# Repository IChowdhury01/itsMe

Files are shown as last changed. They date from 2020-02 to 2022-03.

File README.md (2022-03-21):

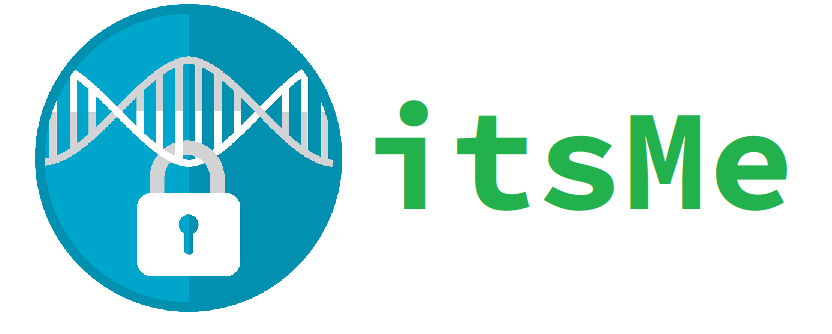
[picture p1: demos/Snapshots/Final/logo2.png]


**A new, revolutionary smart lock.**






# Project Description

itsMe is a smart lock IoT device designed for improved portability and versatility, and low cost-of-installation. itsMe locks can be 3D-printed and assembled at under $60, freely attached onto deadbolt locks with no required home renovation, and controlled remotely via Bluetooth with the itsMe Android app. itsMe's design is fully open-source, and can be modified to fit locks of any size for individual use. See our **[final presentation](https://www.youtube.com/watch?v=xuYFx85O6f8)** and **[complete documentation](/docs/full-documentation)** for further information.

# Demo
**[Operation demo](https://www.youtube.com/watch?v=Y3_GFy8Gmhg)**

**[Rotation demo](https://www.youtube.com/watch?v=DRbHsR_Iyws)**

## 3D-Printable Models

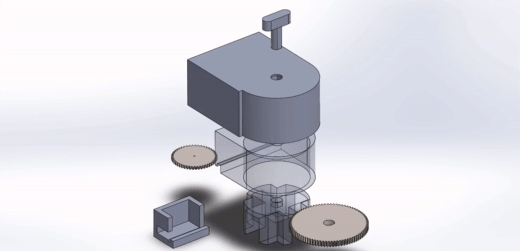
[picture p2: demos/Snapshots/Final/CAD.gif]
CAD Model


Click the animation above to find the models.

# Design

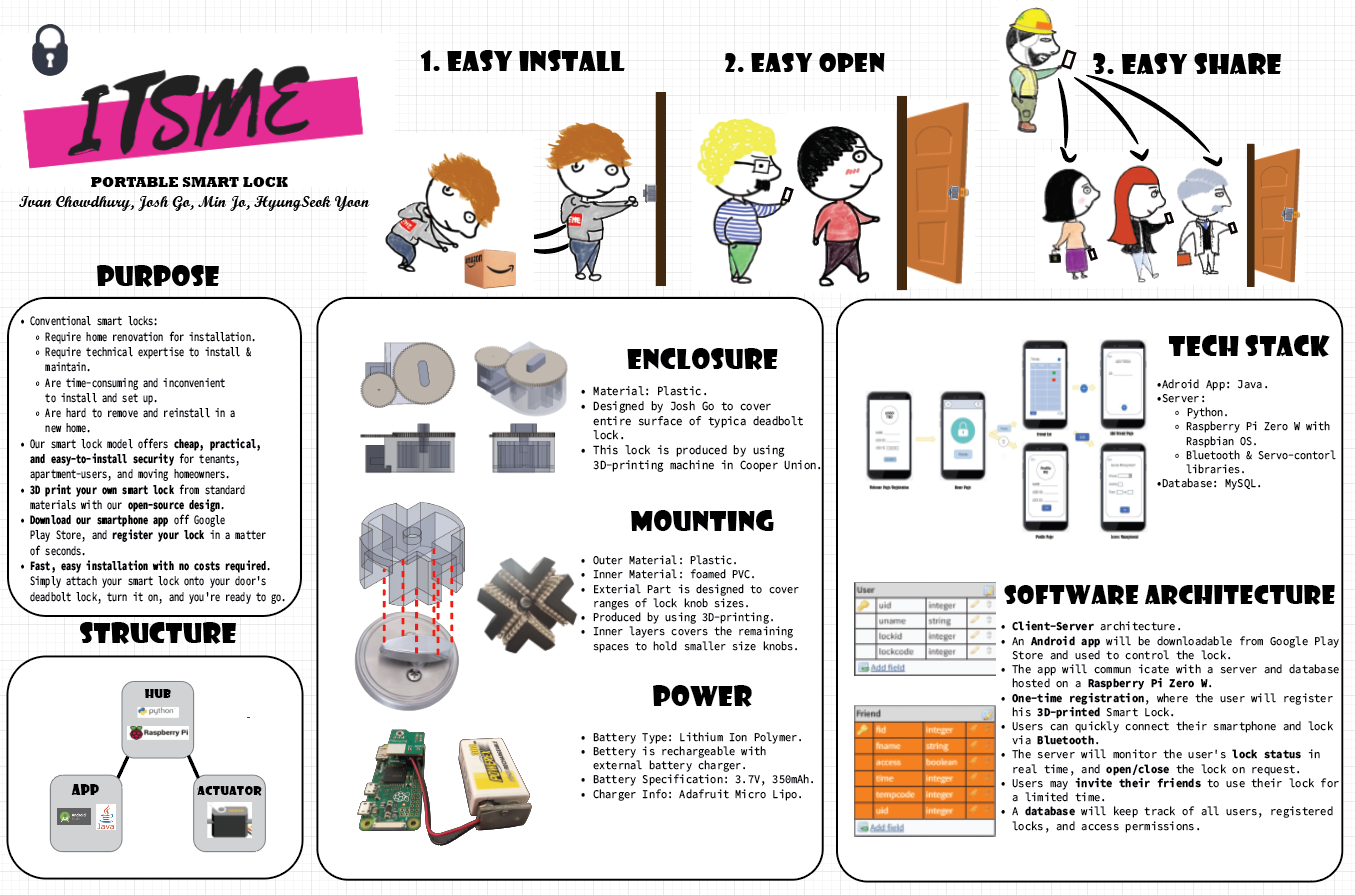
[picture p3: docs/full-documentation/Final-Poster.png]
Design Poster


## Materials


The above materials are all purchasable on Amazon. These are the recommended brands minimizing cost-of-installation; other brands may work, but device stability will not be guaranteed. 

# Getting Started

## Prerequisites
- Android phone
- [Android Studio 4.0+](https://developer.android.com/studio) installed.

## Installation
1. Purchase the materials listed above.
2. Clone this repository
3. [Optional] Modify the dimensions of the downloaded CAD models to suit your needs.
4. 3D print your materials with ABS plastic.
5. Assemble your 3D-printed parts, following the animation above. Place the Servo Motor in the groove and wire it to your Raspberry Pi. Place the self-adhesive tape strips around the edge of your device (where it'll make contact with the door).
6. Open this project in Android studio. Then connect your Android device to your computer with a USB cable, and run the app. Your phone will now have the itsMe app installed.

## Usage
1. Install your smart lock onto your door by simply placing the grip over a pre-existing deadbolt lock. Make sure itthe device is firmly attached to the door with the adhesive strips.
2. Open the itsMe Android app.
3. Turn on Bluetooth on your phone and connect it to your smart lock.
4. Your lock's state is now being monitored through the app. Press the "Lock" or "Unlock" app buttons to control the lock's state. Enjoy!

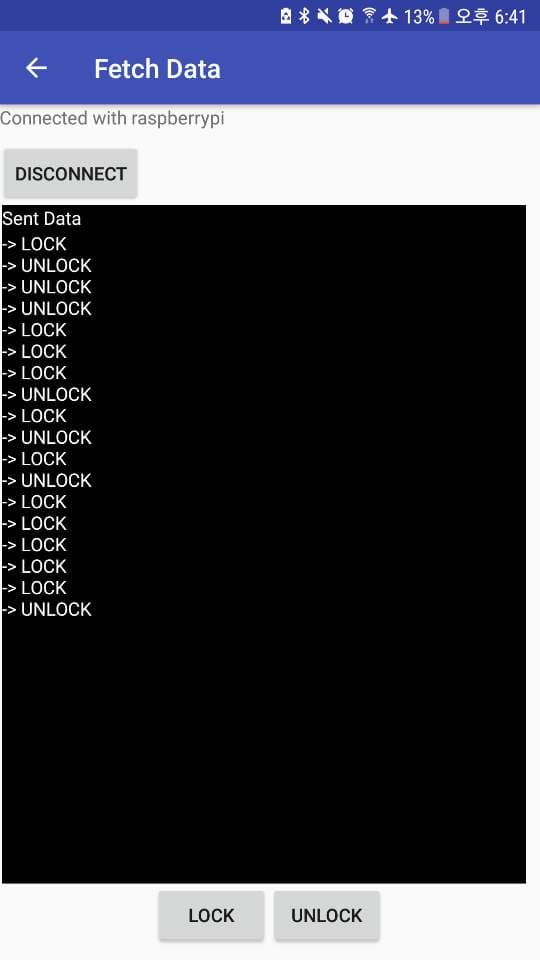
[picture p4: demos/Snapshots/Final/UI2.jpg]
UI


# License

This project is licensed under the MIT License - see the [LICENSE](LICENSE) file for details

# Acknowledgements

- **Development team**: Min JO, Hyungseok Yoon, Josh Go, Ivan Chowdhury
- **Advisors:** Sam Keene, Carl Sable, Shivam Mevawala

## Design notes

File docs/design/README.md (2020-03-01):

# Design Summary

## Purpose

- Conventional smart locks:
  - Require home renovation for installation.
  - Require technical expertise to install & maintain.
  - Are time-consuming and inconvenient to install and set up.
  - Are hard to remove and reinstall in a new home.
  - Have high server-maintenance fees.
- Our smart lock model offers **cheap, practical, and easy-to-install security** for tenants, apartment-users, and moving homeowners.
- **3D print your own smart lock** from standard materials with our **open-source design**.
- **Download our smartphone app** off Google Play Store, and **register your lock** in a matter of seconds.
- **Fast, easy installation with no costs required.** Simply attach your smart lock onto your door's deadbolt lock, turn it on, and you're ready to go.

## Software Architecture

- **Client-Server** architecture.
- An **Android app** will be downloadable from Google Play Store and used to control the lock.
- The app will communicate with a **server** and **database** hosted on a **Raspberry Pi Zero W**.
- **One-time registration,** where the user will register his **3D-printed** Smart Lock.
- Users can quickly connect their smartphone and lock via **Bluetooth**.
- The server will monitor the user's **lock status** in real time, and **open/close** the lock on request.
- Users may **invite their friends** to use their lock for a limited time.
- A **database** will keep track of all users, registered locks, and access permissions.

## Tech Stack

- Android App: 
  - Java
- Server: 
  - Python
  - Raspberry Pi Zero W with Raspbian OS.
  - Bluetooth & Servo-controller libraries
- Database: 
  - MySQL

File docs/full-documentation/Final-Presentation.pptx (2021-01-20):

## ItsMe: Portable Smart Lock

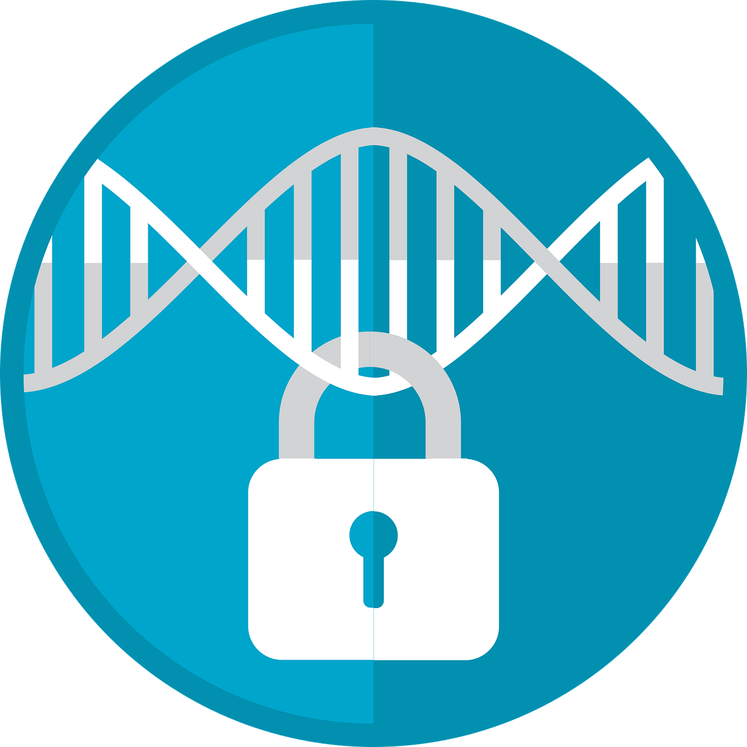
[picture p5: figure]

Hyungseok Yoon, Min JO,
Ivan Chowdhury, Josh Go

## Purpose

- Project: A portable, attachable smart lock for doors with deadbolt locks.
- Catered towards tenants, apartment-users, and frequently moving homeowners.
- Main features
  - Fast, attachment-based installation requires no home renovation.
  - Open-source, modular design
  - 3D-printable
- Other Features
  - Adjustable to most lock sizes.
  - Low manufacturing cost
  - Supports manual and remote unlocking.
  - Android application: used to monitor and lock/unlock door.

## Project Design

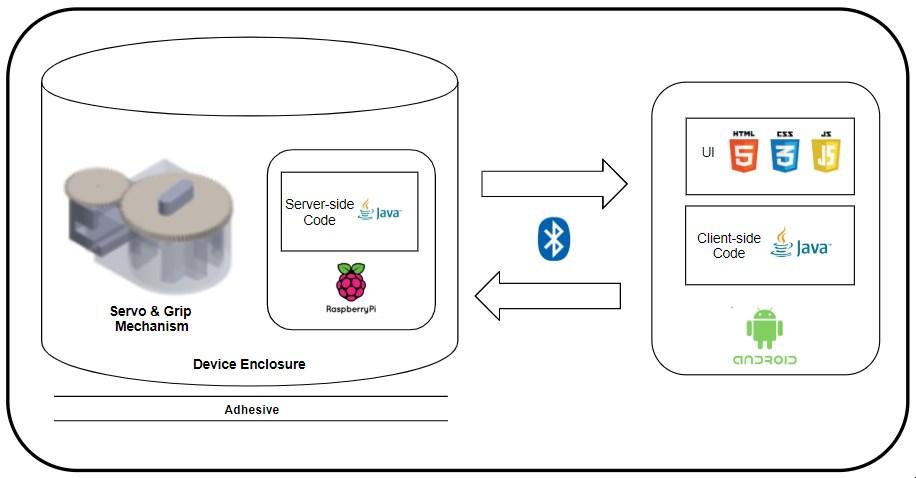
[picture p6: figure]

- App and device communicate via Bluetooth Low Energy
- Raspberry Pi and Servo connected directly.
- 3D-printed gripping mechanism and enclosure.
- Double-sided adhesive tape used to attach onto door.

## Prototype: Specs

- Lightweight:
  - Gripping mechanism: ~150g
  - Overall device: ~250g
- Manufacturing cost: ~$60.00
- Contains slot for Servo motor.
- Smooth-fit groove allows for easy fit with multiple deadbolt lock sizes.
- Manual lock control supported by rotating knob.


## Prototype: Cost of Materials

Material/Process | Cost Estimate
Raspberry Pi Zero W | $10.00
Adafruit Feedback 360° Servo | $27.99
3D-printing (ABS plastic) | $5-10
Strenco 2” Self Adhesive Tape Strips | $13.50

Manufacturing cost: ~$60.00

## Status Update

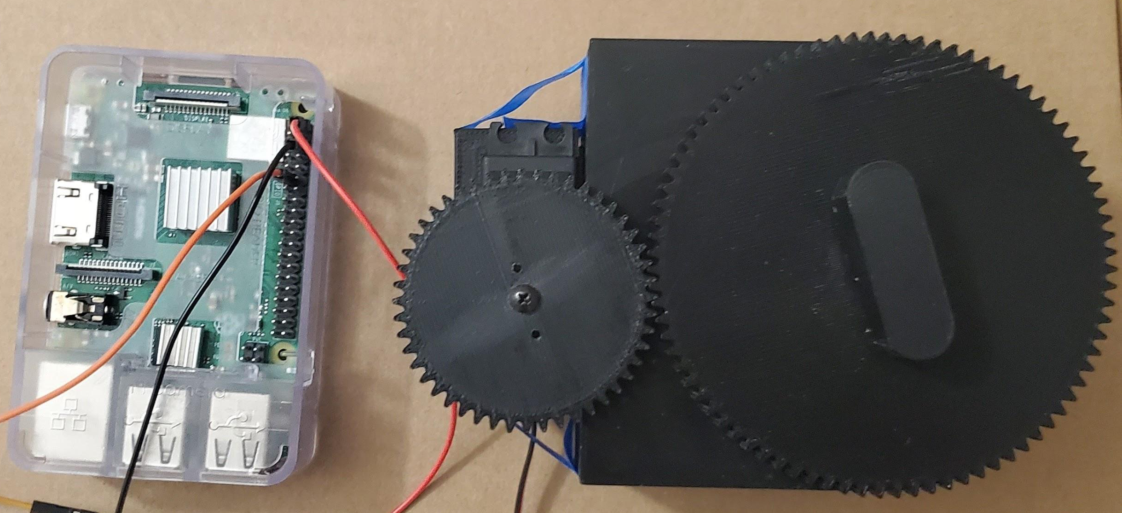
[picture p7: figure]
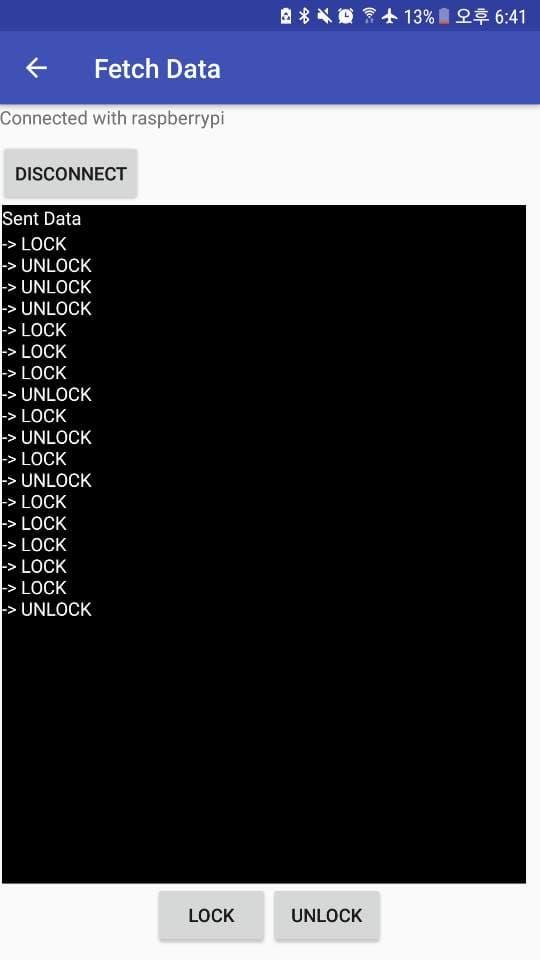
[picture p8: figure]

## Status Update

- First device prototype and Android app beta completed.
- Core features completed:
  - 3D-printable gripping mechanism with open-source design.
  - Gripping mechanism supports multiple sizes of deadbolt locks.
  - Bluetooth compatibility between app and device.
  - Save the lock status.
  - Remote locking/unlocking of door.
  - Low manufacturing cost and lightweight, relative to industry smart locks.
- Features that haven’t been completed yet:
  - Overall device enclosure: Raspberry Pi and Servo/Grip are still separate.
  - Key sharing features.

## Demo

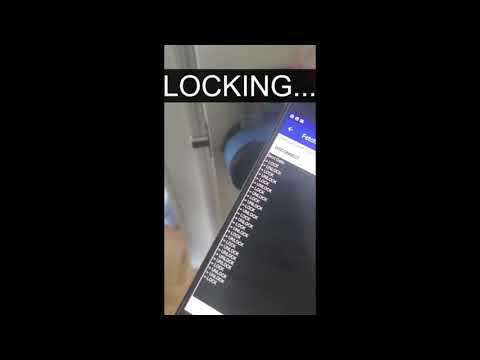
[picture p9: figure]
Cooper Union Capstone Project 2020
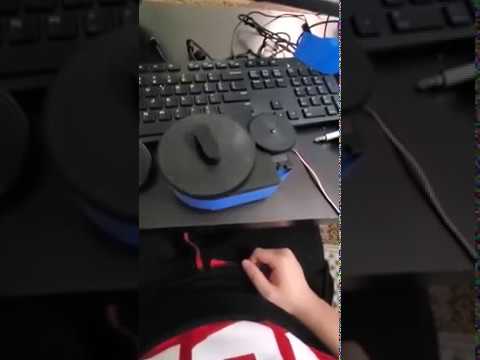
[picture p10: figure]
Cooper Union Capstone Project 2020

## Limitations & Future Work

- Only supports deadbolt locks
- The material is not hard enough so it is necessary to use harder material + different connecting shape.
- Bluetooth Range hasn’t been figured out.
- Auto unlock feature when user is out of control for certain length of time is not yet implemented.
- Software features that can be added:
  - 3D-printed device ID and registration system.
  - Various security measures (e.g. 2-factor authentication)

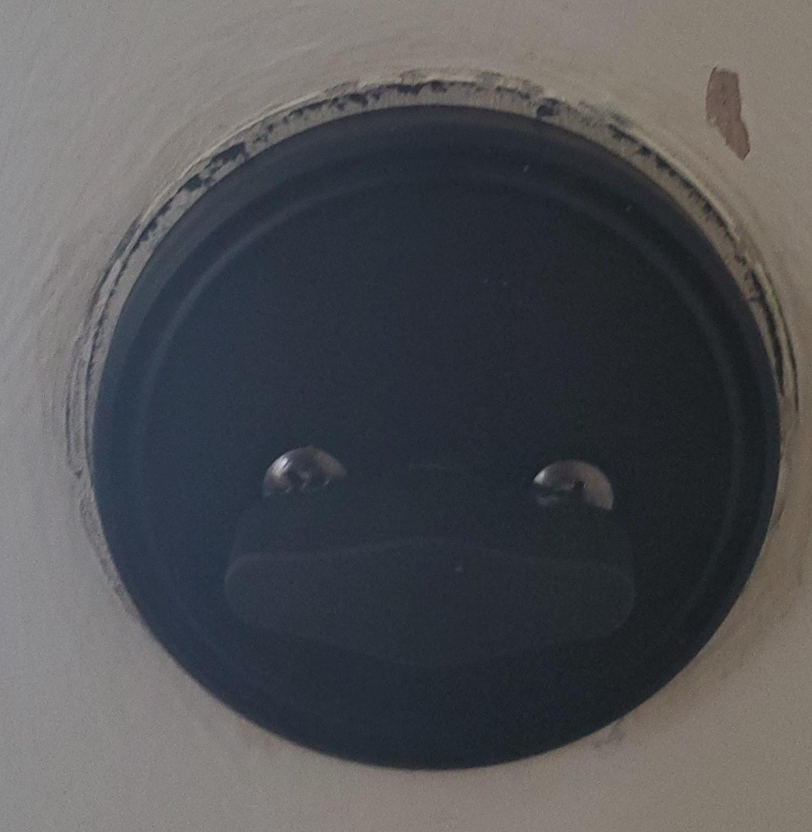
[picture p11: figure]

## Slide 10

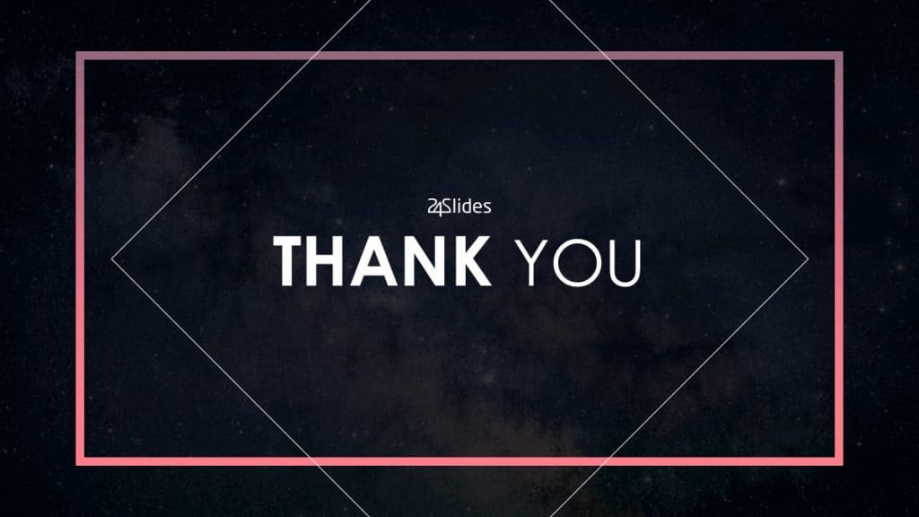
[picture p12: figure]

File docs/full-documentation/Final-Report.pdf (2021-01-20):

### The Cooper Union for the Advancement of Science and Art

### End-of-Semester Report

# _______________________________

# ItsMe: Portable Smart Lock _______________________________

Advisor: | Sam Keene

### Authors:

| Ivan Chowdhury
| Hyungseok Yoon
| Min JO
| Joshua Go

April 10, 2020

## Table of Contents

Table of Contents | 1
1. Abstract | 2
2. Introduction | 3
3. Background | 4
4. Related Work | 9
5. Project Description | 14
5.1. HUB | 15
5.2. Sensor | 16
5.3. Actuator | 16
5.4. Mobile Application | 17
5.5. Physical Device | 18
6. Status | 20
7. Conclusion | 22
Works Cited | 24

## 1. Abstract

As more people integrate smart devices into every facet of daily life, they grow to rely

on the convenience that they offer. Through the internet of things (IoT), devices can be

controlled and information can be collected and shared remotely across a network. One

application of such a system is a door lock, which is used extremely frequently in securing

homes, offices, and vehicles. However, current solutions available to the average person are

difficult and costly to install. The goal of this project is to create a more versatile IoT smart

lock that can attach and detach itself from a wide variety of pre-existing door lock knobs to

allow for easier installation. Along with this comes control via an android application on a

personal smartphone device, while maintaining the existing door lock and key capabilities.

## 2. Introduction

The internet of things is changing the world we live in and is influencing lifestyles in

a plethora of ways. Sophisticated sensors are embedded in physical devices that surround us

which transmit data. IoT is the common language that ties all these devices together into a

network of interconnected devices, where each can gather transmit data to be integrated and

analyzed, then share data to applications to address industry specific needs. This data can

ultimately be used to people’s benefit by improving efficiency and the user experience [1].

One possible application of such a device is the door lock. With a conventional door

lock, keys can be easily misplaced and lost, compromising the important aspect of safety for

the user’s daily life. In addition, access to guests, family, friends and trusted individuals is

cumbersome and requires creating copies of the keys, which too can get misplaced. The

convenience that the internet of things brings to daily life is immeasurable and is a foundation

of the devices all around. Integrating that into the everyday door lock will allow users to

control a lock with a touch of a button through their smartphones, and easily provide their

friends and family access to their homes through their own homes. A device such as this

saves time and effort, which are people’s greatest commodity. Currently implemented

solutions for the IoT-controlled lock, or smart lock, are inherently limited, due to the difficult

and costly installation process that requires home renovation, and the lack of an easy way to

uninstall the device and reinstall it to doors in other homes [2]. The design of our device - the

attachable smart lock - circumvents these limitations and adds versatility and convenience by

allowing the lock to be freely attached to and detached from standard deadbolt locks.

## 3. Background

This section of the report will cover the technical background of our project. We will

introduce the technologies we plan on using, and explain the conceptual details behind the

operation of our project components. The Internet of Things is the notion of creating a

“smart” network of devices that operate in conjunction with one another in real-time. This is

accomplished by placing sensors and actuators on the devices to send signals between them

and a microprocessor, such that the devices can communicate with each other on the same

wireless network [1]. Many IoT projects also involve the creation of an Android application

that communicates with the network, and allows the user an easy way to control the operation

of the network.

An IoT system is generally composed of the following components: a hub, sensors,

actuators, and communication module. The hub serves as the focal point of the smart

network, working as a controller that interacts with all devices on the network, and allows the

user to interact with those devices. Our IoT system will be composed of two main parts: a

Raspberry Pi 3B and an Android application. The Raspberry Pi will serve as our backend

server, and will be responsible for processing and sending signals between devices, in

particular for sending parametrized signals to our rotary actuator in order to rotate the

attached lock between locked and unlocked states. The Android Application will serve as a

UI for users, allowing them to easily monitor the current state of the system, as well as

control the operation of the smart lock remotely [3].

Sensors are physical devices used to monitor the conditions of the environment, to

detect and record information in real time, and to send signals to the hub under certain circumstances. Our system does not incorporate any of these sensors, but improvements can

be made in the future to expand the scope of the system and utilize this extra functionality to

add new features to our smartphone application. Actuators are physical devices that receive

signals from the hub and perform designated physical operations, such as rotation or

switching. For our project, we will utilize Adafruit’s Feedback 360 degree rotation servo as

our actuator. The device is capable of rotating to precise degrees according to the signals it

receives from the hub, is lightweight and provides adequate torque for turning a deadbolt

lock. Lastly, in order to receive the signals being emitted from each device, and provide the

appropriate response within other devices on the network in real-time, a hub is needed. The

hub is essentially a server hosted on a microprocessor, whose role is to mediate

communication between all of the devices on the network; in our case, this includes the Servo

motor, lock device, and Android application [3].

The Raspberry Pi is a single board computer that can be connected to typical

peripherals like, a mouse, keyboard, monitor, and external circuit board. For our IoT system,

we chose to work with the Raspberry Pi 3B+ as our hub. The Raspberry Pi model 3B+ has a

1.4 GHz 4-bit quad-core CPU, 1 GB RAM, Dual-band 802.11ac wireless LAN and Bluetooth

4.2 support, 4 USB ports, Gigabit Ethernet, and support for Linux and Unix operating

systems. Compared to previous versions, it offers support for Bluetooth 4.2 Low Energy,

improved processor speed, and improved wireless and Ethernet connection speed, among

other improvements. The reason this model was chosen over the recently released model 4B

is due to the difference in power usage. The Raspberry Pi 4 has been reported to have higher

power usage, and thus is more susceptible to overheating during usage. We decided to choose

the extra reliability of the model 3B over the improved specs of the model 4B. The Raspberry

Pi 3B is set up through installing a customized copy of Debian (Linux) named Raspbian OS onto the computer through a Micro SD card. From there, the circuit board can be connected

to the required sensors and actuators through jumper cables or wirelessly [5].

An alternative to using the Raspberry Pi as our microprocessor was the Arduino

microcontroller. The Arduino is also commonly used for IoT projects, but has different

specializations and use cases. The Arduino microcontroller is best for use with simple

automated tasks, such as opening blinds, turning on devices, recording and displaying

temperature in real time, and other similar activities. For coordinating a network of devices,

communicating between multiple devices simultaneously, and doing complex time-based

tasks, the Raspberry Pi is more suitable. The Raspberry Pi is also capable of performing

multiple tasks simultaneously, as any computer can do, whereas the Arduino can not. For this

reason, we decided on using the Raspberry Pi as our hub [6].

The physical operation of rotating a deadbolt lock between locked and unlocked states

will be handled by the rotational actuator, or Servo motor, that will be attached to the lock.

The 360 degree feedback Servo used for this is capable of rotating a full 360 degrees, as well

as rotating to specific angular positions, according to the parametrized signals sent to it from

the Raspberry Pi microprocessor. This allows for the rotation of the deadbolt lock to be

remotely controlled from the Raspberry Pi, through code written in Python. The Android

application provides the user with a simple and straightforward way of remotely controlling

the Servo motor’s rotation, through sending signals to it via the Raspberry Pi [7].

It is also essential to choose what type of wireless networking protocol and wireless

signals will be used for inter-device communication within the IoT network. There are a

number of options available for this, some specialized for usage in similar systems. Among

our primary considerations for this were Wi-Fi, Bluetooth, Zigbee, and Z-waves. Wi-Fi is the

most ubiquitously used wireless networking protocol. Its advantages are that it is compatible with almost all devices, including the vast majority of mobile phones and computers, it

supports long-range communication, and provides a strong connection between

communicating devices. It is also easy to provide security to a Wi-Fi network through WEP,

WPA, WPA2, or WPS encryption. Its disadvantages, however, are that it drains battery life at

a faster rate than most other options, and requires a Wi-Fi access point to be in the vicinity.

The next option considered was Bluetooth. Bluetooth’s main advantage is where Wi-Fi lacks

in: | battery | drain. | Bluetooth | provides | easy-to-setup | connections | between

Bluetooth-compatible devices, with very low battery drain relative to Wi-Fi connections.

However, it mainly only works for phones, tablets, a small set of other Bluetooth-compatible

devices, and has a weaker range and connection strength compared to Wi-Fi [3].

The last options considered were Z-Waves and Zigbee radio waves. Both are wireless

networking protocols designed specifically for smart home networks. They offer strong

connections between devices with very low battery drain. Z-waves transmit at 908 MHz,

while Zigbee waves transmit at 2.4 GHz. This means that Zigbee is capable of transmitting

more data, but over a shorter range than Z-Waves. The disadvantages are that there is a high

degree of interference if there are many devices on the same channel. They are also more

complicated to set up, and do not offer the same degree of compatibility across devices as

more general wireless networking protocols do [3].

For our implementation, we will use the IP address assigned by the home router to

communicate with connected mobile devices. Furthermore, we ultimately decided to use

Bluetooth Low Energy (BLE), a wireless technology that emphasizes low cost and low

power, in order to communicate between the user’s smartphone and the server [3]. The reason

for this is because the Raspberry Pi, which will host our server and allow communication

between the user’s android app and the lock, is battery powered. The Raspberry Pi has the ability to last up to an hour on continuous Wi-Fi while powered by a 4000mAh battery. Other

sources reported the Raspberry Pi to last up to 2 hours with a 4000 mAh supply [4]. Because

the device we’re creating is a lock, the server dying after a few hours would be catastrophic,

because it would prevent the user from controlling the lock after only a few hours, potentially

locking them or their guests out of the home. By using BLE, however, the server may last

many days on end. The tradeoff to this is that the stability of the connection between devices,

and the strength of the signals, would be significantly lowered. However, since using the

smart lock only requires the user’s smartphone to be in the immediate vicinity of the lock,

this should not be a significant issue, compared to the battery life issue that would arise from

using Wi-Fi.

## 4. Related Work

The term IoT (Internet of Things) was first invented in 1999 and made its way into the

mass market in early 2014 [1]. Because IoT has been exposed to the market for several years,

there are a plethora of IoT devices available, and hundreds of smart locks, as a simple Google

search shows. To compare smart locks, we introduced two main considerations to determine

the quality of the product: Price and Features.

The term price refers to these parameters:

1. Device Price: Price is measured by summing up the cost of every device and

component that is used. In a smart lock, this includes: the price of the device, the price

of maintaining the server that mediates connections between devices on the network,

and the cost of installation.

2. Cost of Installation: The term cost is measured by how much damage it inflicts on the

door and door lock it is attached to. As mentioned above, our device is intended to

provide support for consumers who are renting or sharing their living quarters. A cost

is therefore applied if the pre-existing home materials must be repaired after the smart

lock has been detached.

There are three key features to consider:

1. Easy Mounting: To lower the cost of the door, this device should adjust itself to the

various heights and sizes of an existing doorknob. The installation and removal

should be easy.

2. Lock/Unlock: Since this device should work remotely, users should be able to lock or

unlock the door lock from a remote distance. Also in the case when users’ phones are

out of battery, the door lock should be able to be locked or unlocked manually.

3. Sharing key: When a registered user tries to invite a guest, he/she needs to be able to

share keys in order for the guest to unlock the door lock. Keys must be sharable so

that another user can access the house.

Depending on the above parameters, the three most similar products are compared in

the table below [2].

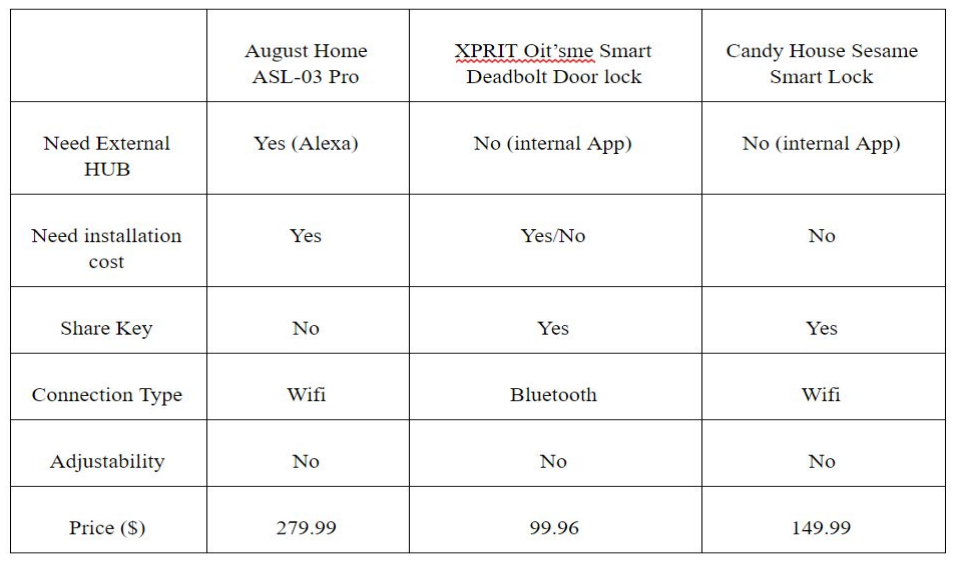
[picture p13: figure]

Figure 1: Comparison of existing smart locks in the market over the decision parameters.

Comparing the existing products in the market, it is clear that most of them have

similar features to what we are trying to build. However, it is also clear that none of the above

solutions is highly adjustable for different sizes and shapes of door locks.

The design of a universal grip, a structure that would allow our device to be freely

attached onto deadbolt locks of varying dimensions and shapes, was derived from the field of

robotics. In industrial robotics, it is necessary to develop a better way to hold an object in

order to manufacture a product. The two most commonly implemented designs we found for

a universal grip are known as the mGrip and the balloon grip.

A balloon grip is a grip which can hold an object with a balloon which is filled with

small particles. It was developed by the Cornell University robotics team and the former

version of the balloon grip was used to hold grounded coffee beans. The mechanism of the

balloon grip is pressing down the balloon to the object and vacuuming the air inside the

balloon so that the balloon can deform and fix the shape to the according object [2].

Similar to the balloon grip, mGrip is a gripping system developed by Softrobotics.

The only difference between the balloon grip and mGrip is what they are using to grip an

object. While a balloon grip uses a balloon to grip the object, mGrip is using silicon based

arms that can flexibly adjust its shape like a human-hand. The mechanism of this process is to

put the grip around the object and pull out the air/liquid that is filling the inside of the grip,

thus making the shape of the grip fixed to the shape of the object [8].

Both methods of gripping are fairly new and well-developed. However, they still pose

certain limitations. One such limitation is that they both require a vacuum state through

suction, which can be difficult to implement [9]. The details and cost of such an

implementation are not published in detail. Furthermore, they are both difficult to implement

within a compact size. In building a smart lock, size is one of the most important aspects of

our design; the device must be small enough for convenient installation and handling.

The online group, hackster.io, supervised a project to build “DIY

smartphone-connected door locks”. The goal of this project was to build a wired version of

the smartphone-connected door lock that can manually close the door lock when the user

sends a signal to the device via an application called Blynk [10]. The main function is the

same for this project: to build a smart lock that can work remotely using a mobile connection.

This product has a compact size, is lightweight, and has a fully functional lock/unlock

mechanism.

While the Blynk-hosted smart lock implementation provides many core features that

we planned for our own device, our design will also introduce new features that may expand

upon their implementation. The key differences between our two products can be classified

into the following three categories: software, hardware, and adaptability.

The software of the hackster.io smart lock implementation relied on a third-party IoT

platform, known as Blynk, to host a server that would control the communication and

behavior of devices on their network [10]. Within our application, however, we will build our

own server and run it remotely from the Raspberry Pi. Our application will also provide

additional features not present in the aforementioned implementation. Within our application,

it would be possible to share a key with friends, granting them temporary access to the lock.

This allows for a user’s friends or family to access their home without the user needing to be

present.

Furthermore, the hardware of our final device will be structured differently from the

hackster.io implementation. We are going to put the overall circuit in the main container and

this will be powered by batteries. The advantage of having a power cord is that this machine will not be turned off, so that consistent service is guaranteed. However, if a door is too far

from the outlet, then this will occupy much space.

The final difference between our two implementations will be adaptability. In the

hackster.io project, they 3D printed the shape of the knob so that it only works on the specific

dimension and sizes of a single door that was used for testing [10]. However, the structure

used for our design will be more adaptable to variance within the shape and dimensions of the

deadbolt locks it will be attached to.

## 5. Project Description

Our final product is a freely attachable smart lock IOT device, which can be easily

attached onto any conventional deadbolt door lock. Once attached, by using the mobile

application, the user will be able to automatically lock/unlock the door and get the lock

status updated. Overall, just like the conventional IOT system, our IOT system will include

four main components: a HUB to receive and transmit signals between devices on the

wireless network, a sensor to interact with the HUB, actuator to implement the function and a

user friendly mobile application. The physical device of the smart lock will contain the sensor

and the actuator of the system and implement the lock/unlock process by the attached grip.

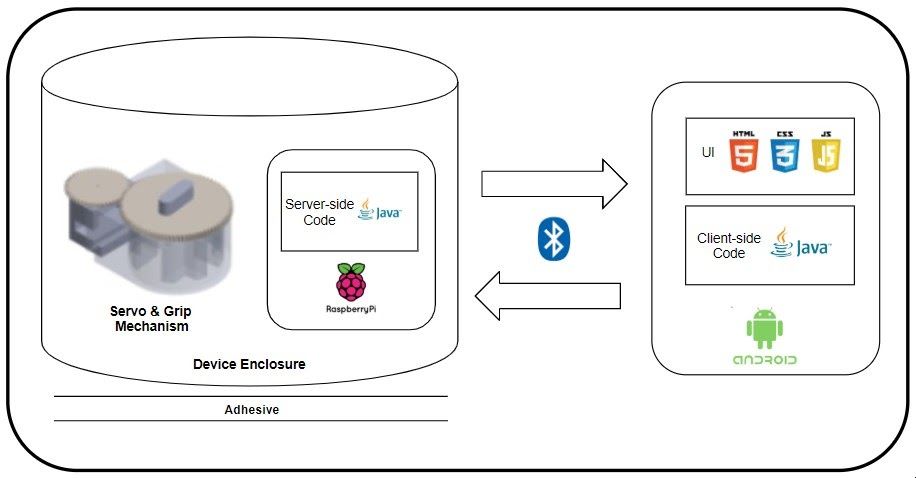
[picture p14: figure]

Figure 2: A diagram outlining the architecture of our system

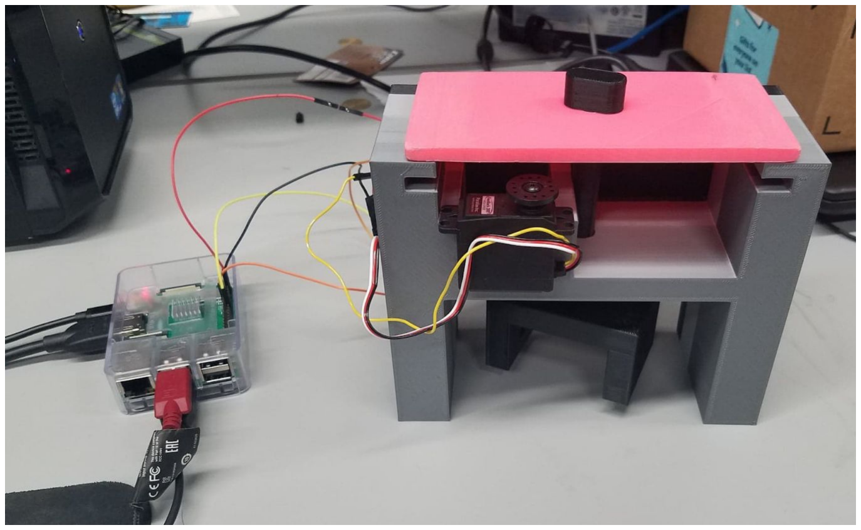
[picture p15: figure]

Figure 3: Prototype 1 Setup

### 5.1. HUB

The HUB of the IOT system makes the connection between all the components of the

system. We have decided to use the Raspberry Pi3, which is a single-board computer that can

run the Linux operating system and be programmed with Python, to host a server that will

handle inter-device communication and signal handling. This will be the core component of

our hub. All communication will occur between this server and mobile devices connected to

the network. When the server receives a request from a user to manually control the lock, it

will operate the Servo motor, which is directly connected to the Raspberry Pi, to rotate the

direction and amount required to shift the lock’s state.

### 5.2. Sensor

The biggest advantage of constructing a stable IOT system is that we can easily add

any functions by simply connecting an appropriate sensor to the HUB. Currently, we have

decided to use a position sensor to fully complete the capabilities of the lock. Using the built in position sensor of the servo motor, we can easily track the change of the motor position

through an angular value. When the user first sets up the smart lock and goes for the

lock/unlock process for initialization, the HUB will automatically store the status of

lock/unlock in a form of angular value. The stored value for a certain type of the lock will

then be used to interact with the actuator to make it serve the commands from the user. As for

other types of sensors that we deemed appropriate for future expansion, functionality such as

fire safety and air quality/carbon monoxide detection through the use of a DS18B20

temperature sensor and an MQ7 sensor. The sensor will be continuously gathering data which

will ultimately expand the functionality of the IoT system.

Another possible use case for implementing sensors would be to allow the lock to

detect when the user exceeds a certain distance from the lock, after it’s attached to the door.

The device may be programmed to automatically lock itself once this limit is exceeded. We

named this the “automated lock” function, and have considered implementing it as a stretch

feature for our device.

### 5.3. Actuator

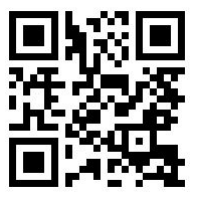
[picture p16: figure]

Figure 4: QR code for the link to Actuator demonstration

The main function of the smart lock is making the lock to rotate, while the grip of the

physical device holds the lock the actuator and will make the actual rotation by getting the

command code from the HUB. At first we were trying to implement a normal servo motor, but this actually caused a problem as normal servo motors only serve a 180 degree rotation.

We realized that for many types of locks the rotation angle requires value over 180 degrees.

To solve the issue we decided to use the Parallax Feedback 360 Degree High Speed Servo,

which can provide a continuous rotation for both directions. The rotation of the motor is

managed by a program coded with python. When testing the prototype we focused on the

stability rotation, so we also checked the delay between the change of rotational direction

(approximately 0.5second) to decide an appropriate sleep time between the continuous signal

from the mobile application.

### 5.4. Mobile Application

For easy use of the smart lock, a mobile application will be provided along with the

physical device. The app was developed using Android Studio and is connected with the

Raspberry Pi using bluetooth. When using the application, to address the security issue, the

user will be allowed to create an account, whose information will be potentially encrypted

and stored in a database. When the user finishes the installation of a physical device and login

with a created account, the guideline for initialization will show up. The initialization will

require the user to first rotate the lock manually to store the data of lock/unlock status. Once

the initialization is finished the mobile app will display the lock’s current status (locked or

unlocked). The user can change the lock status by simply clicking the icon that indicates the

lock status.

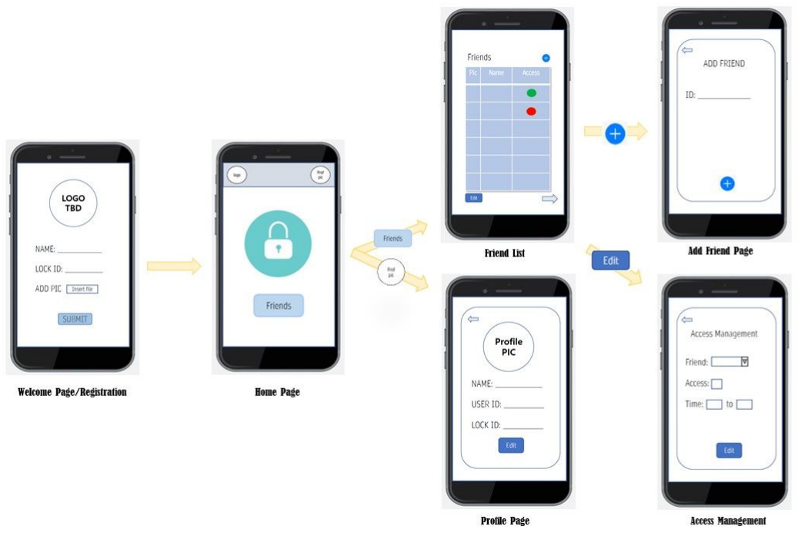
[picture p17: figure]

Figure 5: Map for the Mobile App UI

The app also enables the users to manage friends lists. Once the user adds friends,

users can send a temporary access code which is used to manage the smart lock for a preset

time period. The status of the access approval for each of the friends will be shown in the list

and can also be edited in the same page. The temporary access code will be generated each

time the users decide to share their authorization and will be deleted once the preset time

passes. Users may also edit the profile info whenever needed. To enable the users to keep in

track of the battery status of the Raspberry Pi, the app will be showing the status in the main

page of the app, this will prevent users from problems occuring due to the low battery.

### 5.5. Physical Device

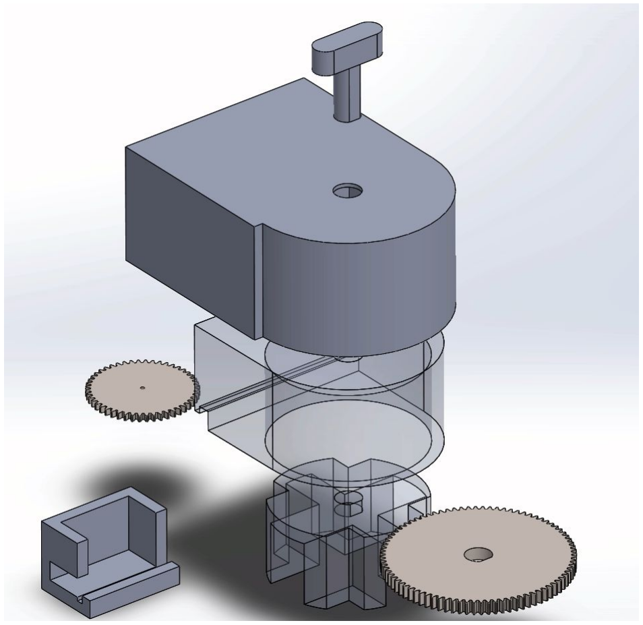
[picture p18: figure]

Figure 6. Final Prototype Design (Exploded View)

### 5.5.1. Design Description

Our physical model consists of the adaptive grip and rotational structure. All the

components of the physical device are 3D printed except Raspberry pi and grip. The main

goal of this device is to be attachable to any type of the doors and to be adjustable with

various dimensions of conventional deadbolt locks. As shown in the figure above, our final

prototype looks like ‘Jimmy Proof Deadbolt lock’. Figure 6 (a) is the shape of what ‘Jimmy

Proof Deadbolt lock’ looks like, and Figure 6 (b) shows how our prototype design looks like

in Solidworks. The reason for this prototype model is to effectively cover the existing

deadbolt lock design. According to the structure, most of the conventional door locks are just

a circular design. Additional rectangular space for the raspberry pi and the servo motor is

accommodated on the enclosure. When all parts are connected, the prototype will be attached

to the door using 3M’s double sided tape, which can hold upto 90 pound per inch.

### 5.5.2 Rotation Mechanism

Conventional deadbolt door locks have a rotational mechanism in which a user just

rotates the door knob to open/close the lock. By research, most of the deadbolt locks are in an

‘open’ state when the knob is turned to the right, and ‘close’ state when the knob is turned to

the left. To control the rotation, Parallax’s ‘continuous rotation servo motor’ will be used.

When the servo is installed, two rotating gears will connect the servo with the grip. Since two

linked gears will have opposite rotational direction, installation of our model should be

guided. Also, in order to have a steady rotation, larger gear will be used to rotate the grip to

make the lock rotate slower. The ratio between small and large gear is 4:7, allowing a higher

torque to be yielded in turning the lock knob.

### 5.5.3. Grip Mechanism

There have been lots of attempts to develop a method to grab universal shapes with

one device. The original attempt for this project was to import one of those methods to grab

various shapes of conventional deadbolt locks. However, it was difficult to implement those

technologies due to weight limitation. In order to be attached on the door perpendicular to the

axis, it was necessary to make it as light as possible to ensure safety and convenience.

Technologies that we have under consideration were elaborated in the previous sections.

This Figure on the right is called ‘door knob grip’,

completely made with silicon and helps to open the door knob

easily by increasing the surface area and resistance. Silicon or

other soft and elastic materials were considered to be used since it

was necessary to adapt to various sizes.

Our final model for the grip looks like the figure on the

right. There are two different sections for the grip; narrow and

wide. This area depends on the size of the door knobs. Then the

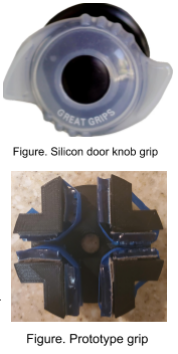
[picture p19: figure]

grip is filled with silicon gel which is used as a supportive insole of

the shoes. When the door knob is inserted, the silicon gel is filling

the rest of the area so that it effectively holds the knob. The size of the knob is varying so the

minimum width and maximum width is based on our neighborhoods’ door knob sizes.

## 6. Status

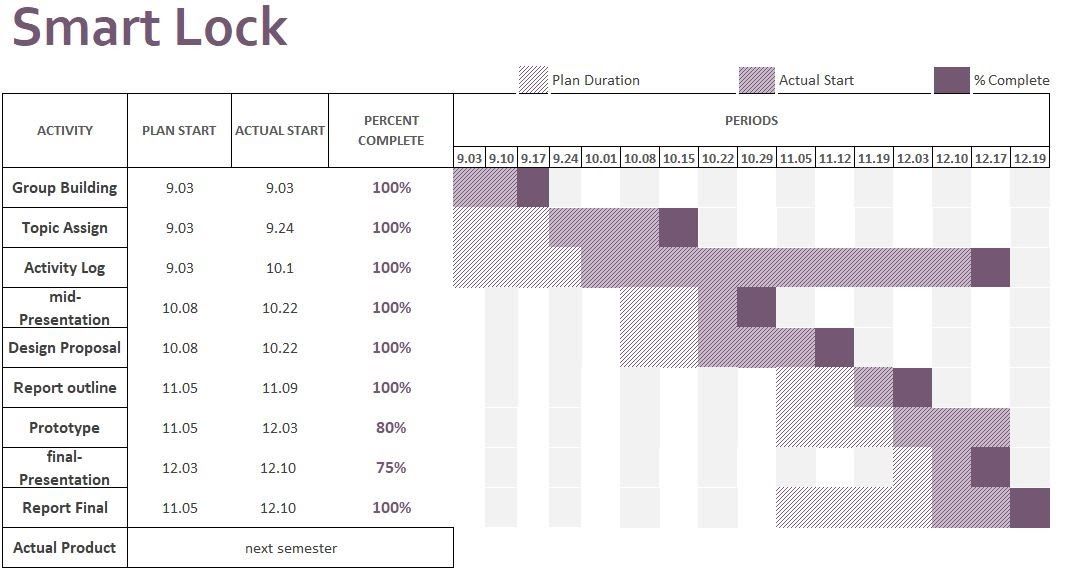
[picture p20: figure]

Figure 7: Fall 2019 Activity Log

The above figure displays a Gantt Chart modeling our work timeline for the Fall 2019

semester. During the group building and topic assignment phases, we formulated our group

and brainstormed on a project to work on. This phase took longer than it for most groups,

because our group wasn’t finalized until 3-4 weeks into the fall semester. The

mid-presentation and design proposal stages highlight the time spent finalizing our design

and presenting it to our peers and faculty. After this phase, we outlined and drafted our

end-of-semester report, and began the building phase for a first prototype. By the end of the

fall term, the first model for our lock-gripping mechanism was designed and 3D-printed, our

Raspberry Pi was set up and configured with the Raspbian operating system, and a basic

script was configured to operate the Servo motor.

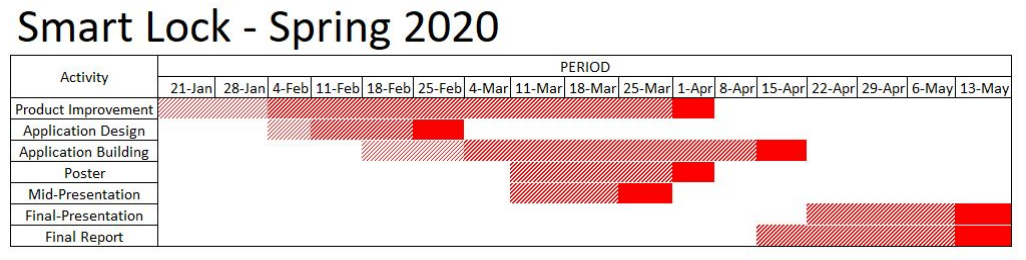
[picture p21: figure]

Figure 8: Spring 2020 Activity Log

The figure above was the plan for the most recent semester. We have finished our

product improvement, application design process and so on. Due to the school being

inaccessible, the device is not completely polished, but it has been finished in an appropriate

amount and serves its foundational purpose. The code and 3D design will remain as an open

source so that anyone who wants to access our design can download and print out the part

and all the components used in this project will be recorded. Video of the demo and installation guide will be documented in order to know how our product would work in the

market if any further improvements are made. The figure below shows the current device.

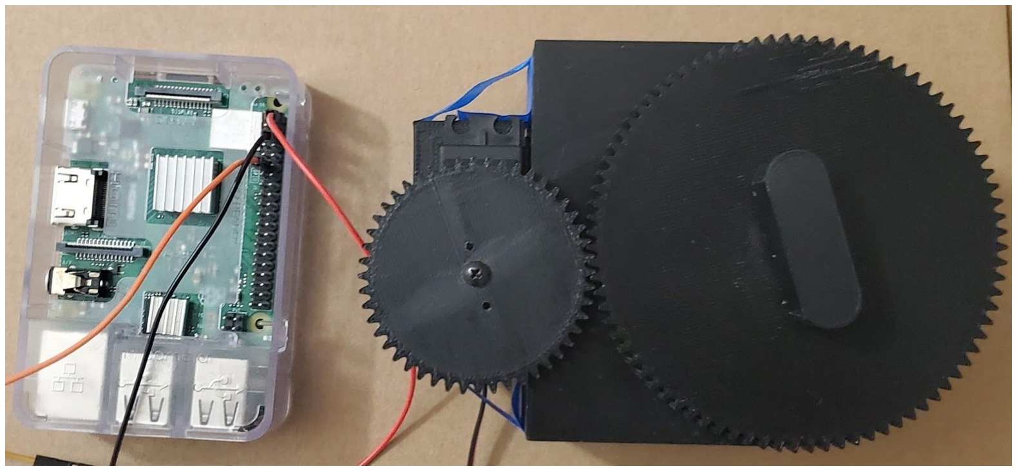
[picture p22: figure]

Figure 9. Final Prototype

## VII. Conclusion

The purpose of this project is to create a smart lock device that can be freely attached

onto any conventional deadbolt lock. The user can then remotely control the lock through the

accompanying Android application. The motivation behind this project was that many

conventional smart lock devices currently in the industry pose challenges in cost and

adaptability, particularly in the flexibility of installing and reinstalling the lock, and the costs

required to purchase, install, and maintain the lock. This design attempts to provide a

cost-efficient, reliable, and easy-to-install smart lock that is practical to use for all users, and

does not require home renovation or expensive server maintenance costs to use.

The project is an Internet-of-Things system containing a hub, actuator, and

communication devices. A Raspberry Pi model 3B+ was used in conjunction with a

smartphone application for the hub, and will be responsible for handling bluetooth signals

sent between the various devices on the network. A 360 degree feedback servo motor will be

used for the precise angular rotation of the deadbolt lock that the device will be attached to,

into locked and unlocked states.

At this juncture, the mechanical design and the software designs have been fully

integrated into a working final prototype. While many more improvements can be made, the

inability to access important resources at our institution hinders us from fully achieving all

the intended goals and vision.

## Works Cited

1. Knud Lasse Lueth. “Why the Internet of Things is called Internet of Things: Definition, history, disambiguation”. Iot-analytics.com. https://iot-analytics.com/internet-of-things-definition/ (12/16/2019)
2. Various Smart Lock implementations in the industry, https://www.amazon.com/August-Smart-Lock-Connect-technology/dp/B0752V8D8Dhttps://www.amazon.com/XPRIT-Oitsme-Smart-Deadbolt-Door/dp/B07WPFZBV5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 (https://www.amazon.com/XPRIT-Oitsme-Smart-Deadbolt-Door/dp/B07WPFZBV5) https://www.amazon.com/CANDY-HOUSE-Sesame-Enabled-Champagne/dp/B0763MY9NG?th=1 (https://www.amazon.com/CANDY-HOUSE-Sesame-Enabled-Champagne/dp/B0763MY9NG?th=1)
3. Bell, Tyler, et al. Smart Sense. 2016, Smart Sense.
4. Moll, Luke, et al. “How Long Does the RPi Last on a Battery?” Raspberry Pi Stack Exchange, 3 July 2014,
raspberrypi.stackexchange.com/questions/19812/how-long-does-the-rpi-last-on-a-batt ery
5. Hattersley, Lucy. Raspberry Pi 4 vs Raspberry Pi 3B+. The MagPi Magazine, 1 Oct. 2019, magpi.raspberrypi.org/articles/raspberry-pi-4-vs-raspberry-pi-3b-plus.
6. Alisa. “Raspberry Pi or Arduino – Which Is Best for IoT Home Solutions?” Seeedstudio, 1 Jan. 2019,
www.seeedstudio.com/blog/2019/01/29/raspberry-pi-or-arduino-which-is-best-for-iot-home-solutions/. (http://www.seeedstudio.com/blog/2019/01/29/raspberry-pi-or-arduino-which-is-best-for-iot-home-solutions/)
7. Block, Michael, and Derek Toub. AFLAT: Automatic Fast Locking Actuated Tuner. 2013, AFLAT: Automatic Fast Locking Actuated Tuner.
8. Anne Ju. “Balloon filled with ground coffee makes ideal robotics gripper”. news.cornell.edu.
https://news.cornell.edu/stories/2010/10/researchers-develop-universal-robotic-grippe r (https://news.cornell.edu/stories/2010/10/researchers-develop-universal-robotic-gripper) (11/05/2019)

9. Eugene Demaitre. “mGrip modular gripper is Soft Robotics’ response to user needs”. Therobotreport.com.
https://www.therobotreport.com/mgrip-modular-gripper-soft-robotics/ (12/04/2019)
10. Hacker Shack (Hackster.io), “How to Make a Smartphone Connected Door Lock”, (Jan 17, 2017). Accessed Dec 10, 2019. [Online Video]. https://www.youtube.com/watch?v=bAcK80fm1_0

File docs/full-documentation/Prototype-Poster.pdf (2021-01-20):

# LET YOUR KEYS FREE

# BACKGROUND

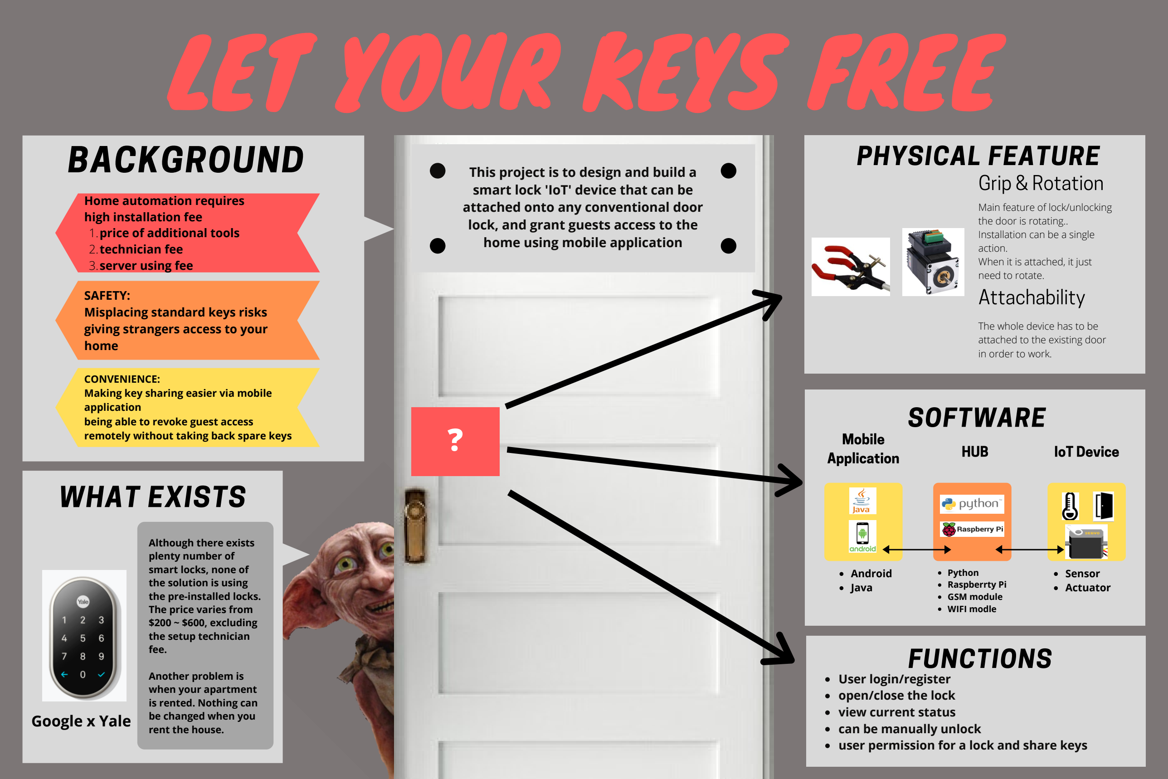
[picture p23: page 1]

### price of additional tools technician fee server using fee

### Home automation requires high installation fee

1.
2.
3.

### SAFETY: Misplacing standard keys risks giving strangers access to your home

CONVENIENCE:
Making key sharing easier via mobile application
being able to revoke guest access remotely without taking back spare keys

## This project is to design and build a smart lock 'IoT' device that can be attached onto any conventional door lock, and grant guests access to the home using mobile application

## WHAT EXISTS

## Google x Yale

Although there exists
plenty number of
smart locks, none of
the solution is using
the pre-installed locks.
The price varies from
$200 ~ $600, excluding
the setup technician
fee.

Another problem is
when your apartment
is rented. Nothing can
be changed when you
rent the house.

## PHYSICAL FEATURE

Grip & Rotation

Main feature of lock/unlocking the door is rotating..
Installation can be a single action.
When it is attached, it just need to rotate.
Attachability

The whole device has to be attached to the existing door in order to work.
?

## SOFTWARE

Mobile

Application

HUB | IoT Device

Android
Java

Python
Raspberrty Pi
GSM module
WIFI modle

Sensor
Actuator

## FUNCTIONS

### User login/register open/close the lock view current status can be manually unlock user permission for a lock and share keys

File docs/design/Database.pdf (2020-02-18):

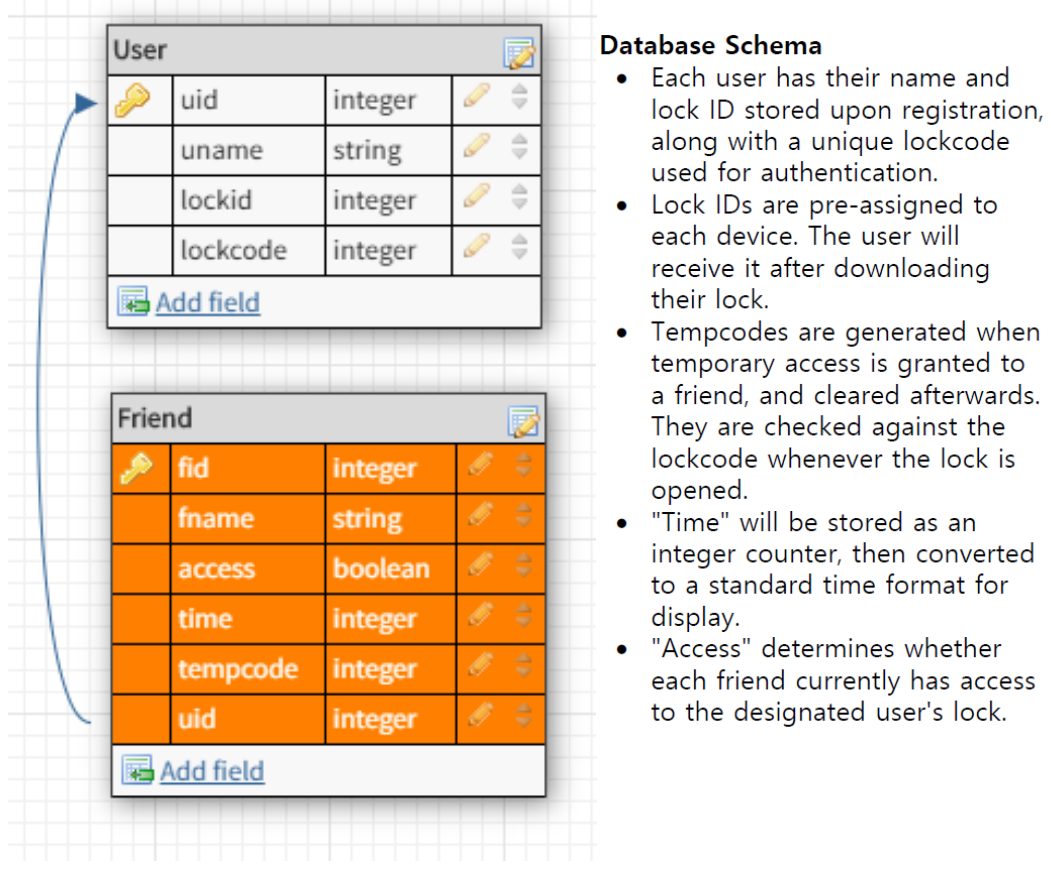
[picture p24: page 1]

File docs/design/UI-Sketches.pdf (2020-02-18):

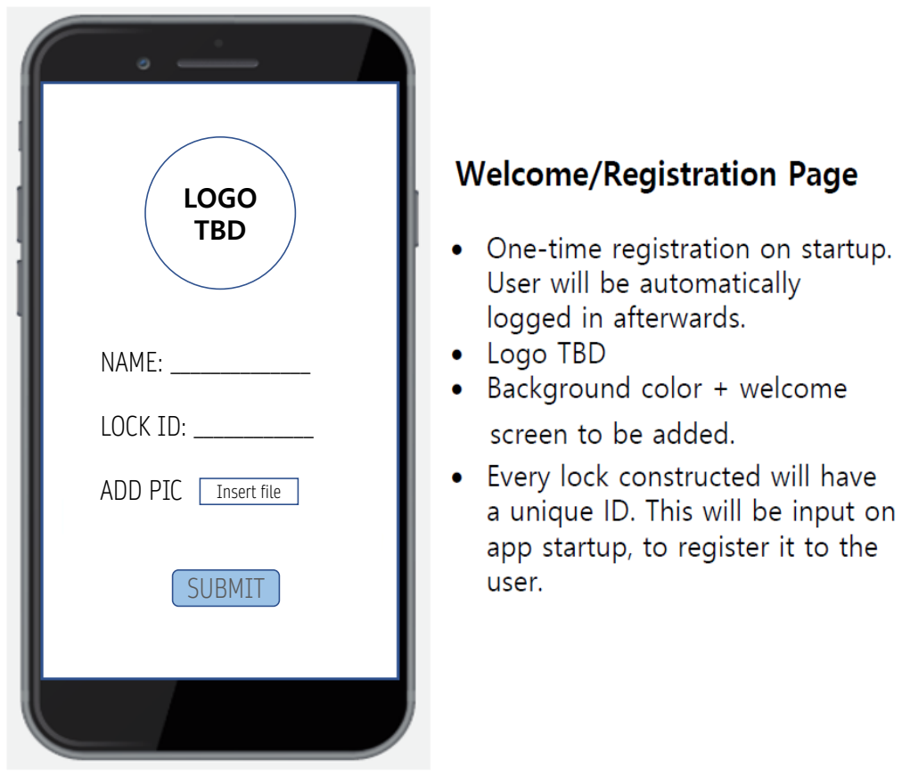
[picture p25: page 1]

NAME: ______________

LOCK ID: ____________

ADD PIC

LOGO
TBD

Insert file

SUBMIT

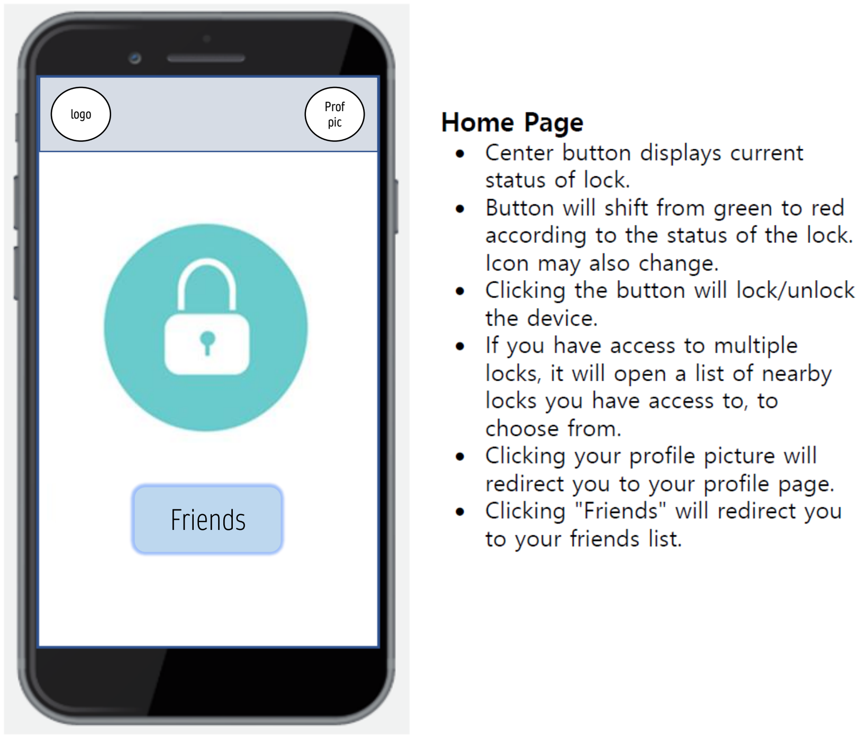
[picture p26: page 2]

Friends

logo | Prof pic

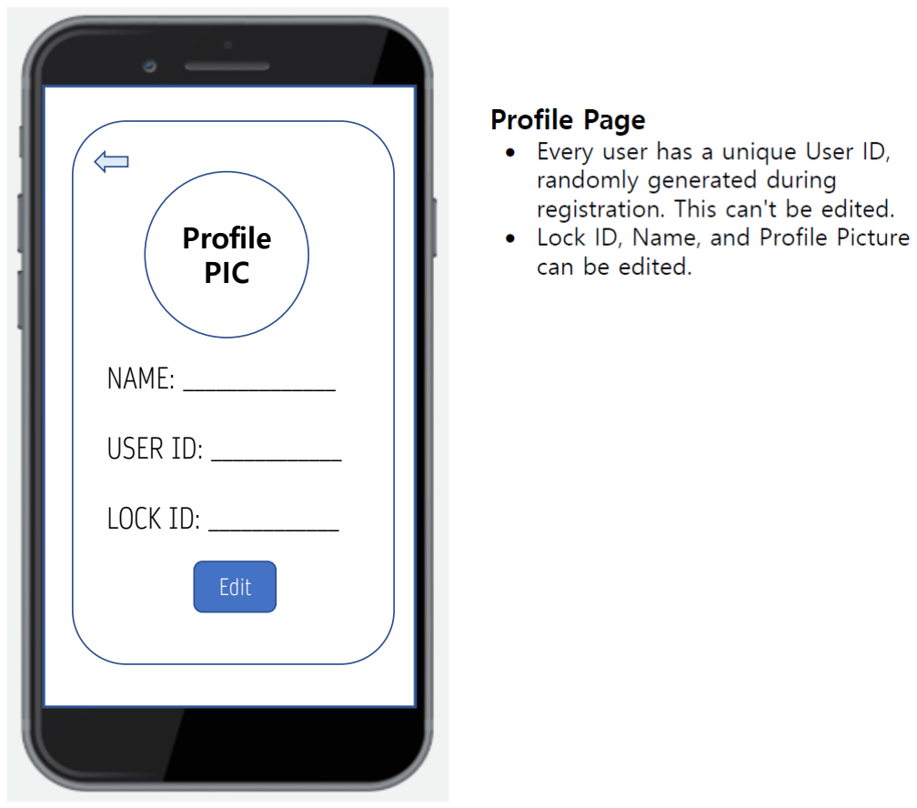
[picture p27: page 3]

NAME: ______________

USER ID: ____________

LOCK ID: ____________

Edit

Profile
PIC

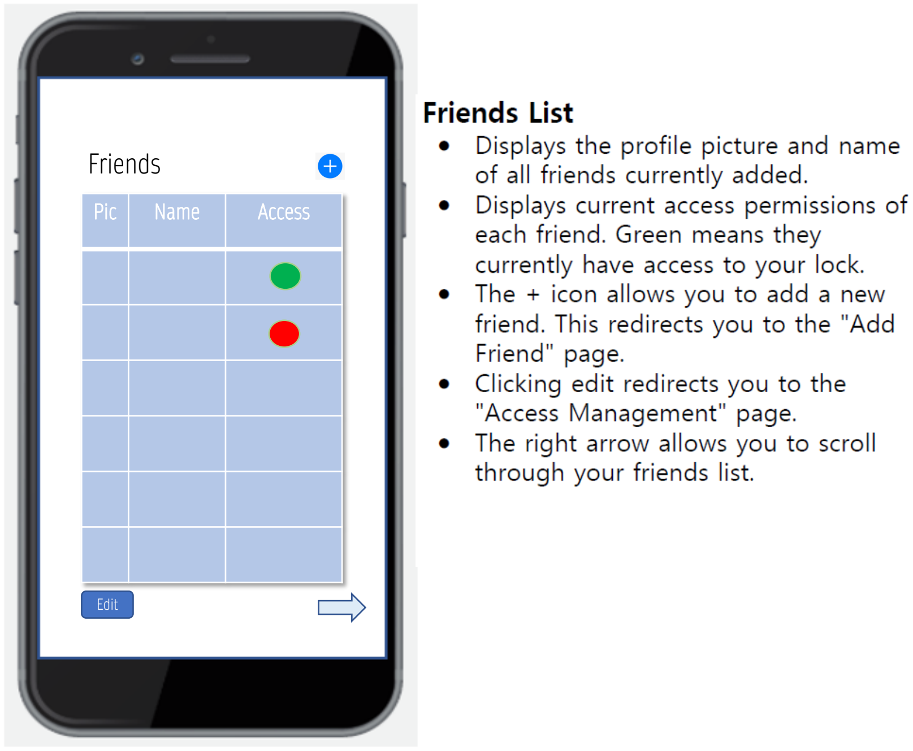
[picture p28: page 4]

Pic | Name | Access

Friends

Edit


ADD FRIEND

ID: ________________


Edit

Friend:

Access:

Time: to

Access Management

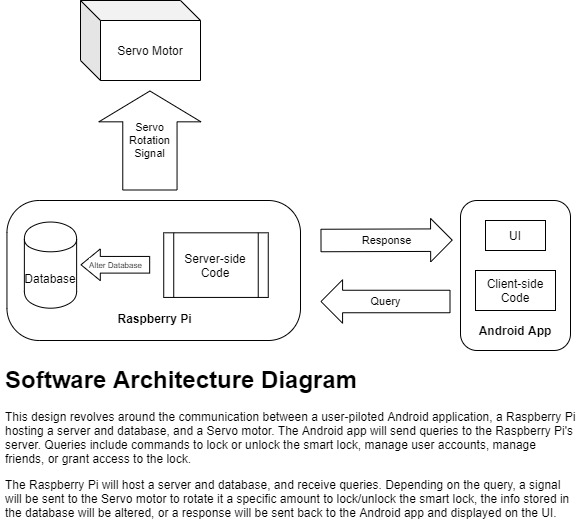
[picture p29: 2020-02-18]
docs/design/Software Architecture.jpg

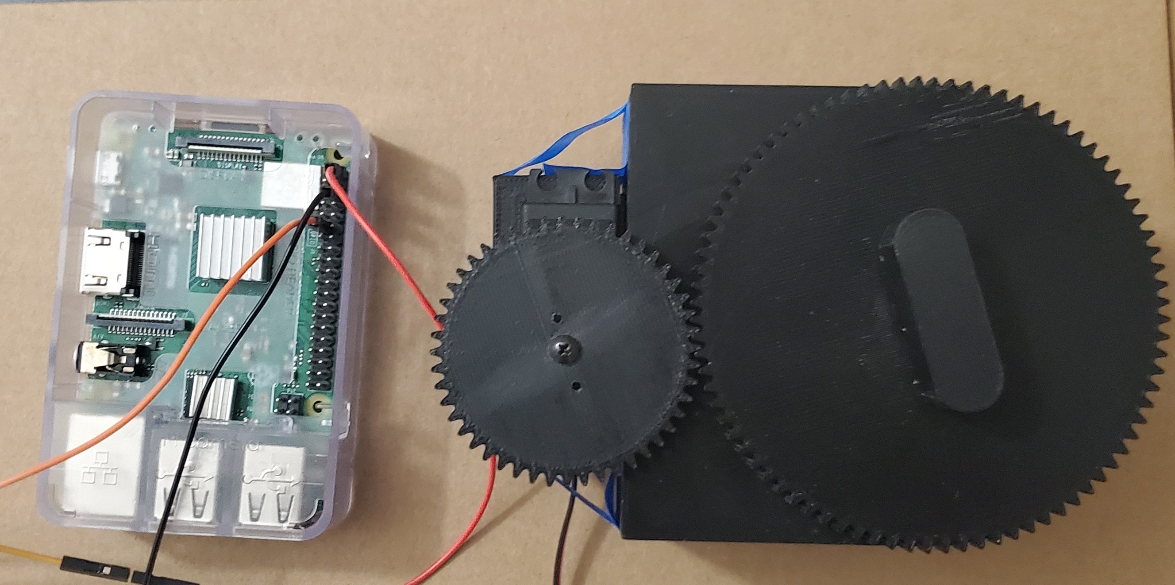
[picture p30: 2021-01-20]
demos/Snapshots/Final/Hardware.jpg

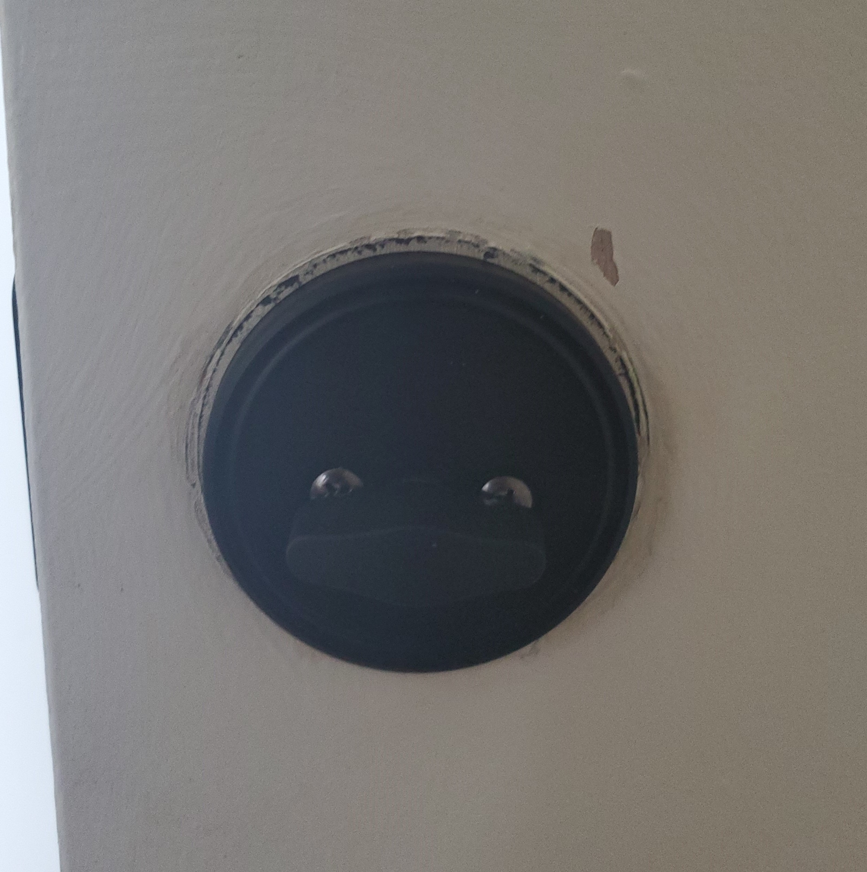
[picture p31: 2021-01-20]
demos/Snapshots/Final/HardwareAttached.jpg

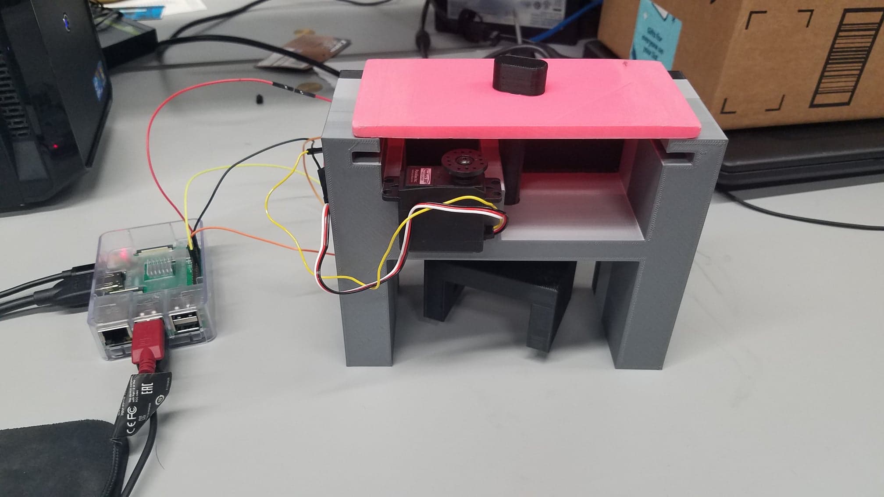
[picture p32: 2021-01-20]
demos/Snapshots/Prototype/Device.jpg

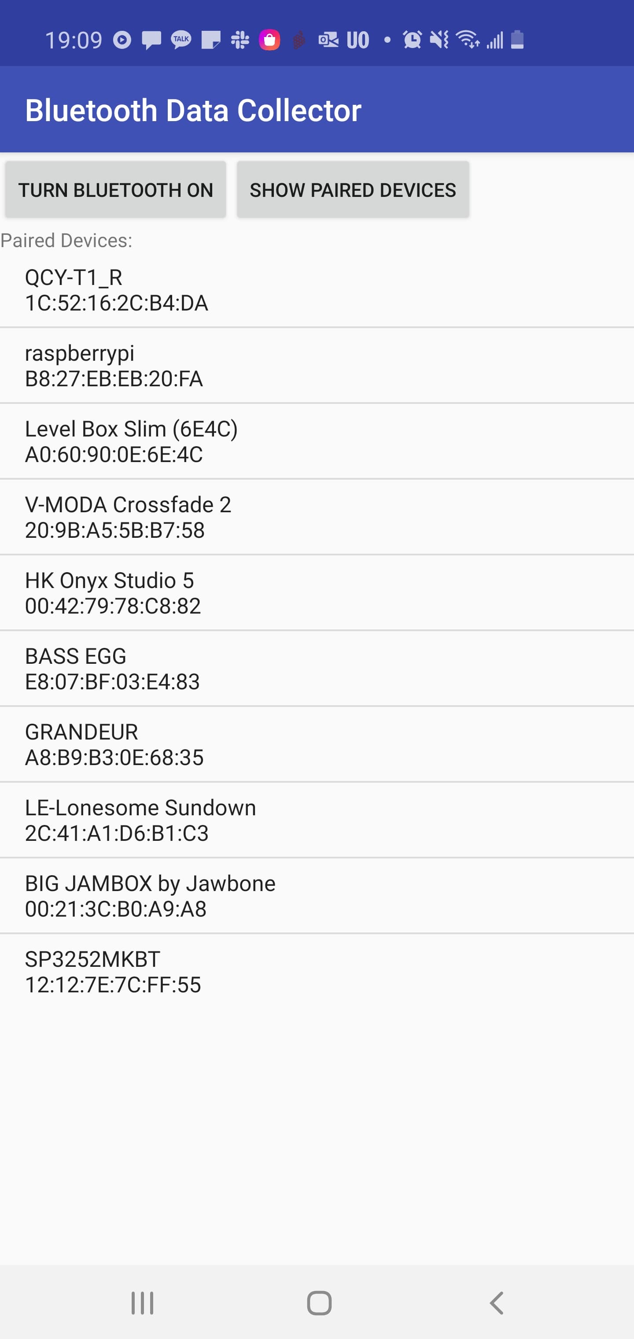
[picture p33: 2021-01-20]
demos/Snapshots/Final/UI1.jpg

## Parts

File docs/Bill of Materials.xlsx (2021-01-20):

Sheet: Sheet1
Material name | Quantity | Price($) | Link | Notes
Raspberry Pi 3B+ Kit | 1 | $69.99 | Amazon (https://www.amazon.com/CanaKit-Raspberry-Premium-Clear-Supply/dp/B07BC7BMHY?s=electronics) | Cheaper. Better reviews. Weaker specs, but less chance to overheat. Also, all the IoT project reports used older models, so RPI4 isn't needed. Missing some items (like MicroSD card)
Amazon_basic_deadboltlock | 1 | $12.39 | Amazon (https://www.amazon.com/gp/product/B07J4VQCL7/ref=ppx_yo_dt_b_asin_title_o00_s00?ie=UTF8&psc=1) | Bought for demonstration
Adhesive Black Hook and Loop Tape | 1 | $12.89 | Amazon (https://www.amazon.com/gp/product/B00H3R9S1K/ref=ppx_yo_dt_b_asin_title_o00_s00?ie=UTF8&psc=1)
 | total | $103.72
Feedback 360 Degrees_Servo | 1 | $41.54 | Adafruit (https://www.adafruit.com/product/3614)
HDMI cable + SD card | 1 | $33.15 | Staples
 | total | $178.41

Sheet: Sheet2
Considering
HM-10 Bluetooth 4.0 Module | 2 | $5.06 | Aliexpress (https://www.aliexpress.com/item/32672670920.html?src=google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) | If one of the devices is battery-powered (like the sensor), we should use Bluetooth for it instead of Wi-Fi. If we use Wi-Fi, it'll run out of power too quickly.
Arduino
Raspberry Pi 4 Kit | 1 | $99.99 | Amazon (https://www.amazon.com/dp/B07VDGKN51/ref=cm_sw_r_fm_apa_i_ajIPDbVHM0V5A) | RPi 4 runs hotter than 3, might overheat. We might want to get the RPi 3B+ instead.
GSM/GPRS Module
Long-Range Distance Sensor |  |  |  | Stretch goal: If the user is a certain distance away from the lock, it will automatically lock.
Motor Driver
Raspberry Pi 3B+ Kit | 1 | $69.99 | Amazon (https://www.amazon.com/CanaKit-Raspberry-Premium-Clear-Supply/dp/B07BC7BMHY?s=electronics) | Cheaper. Better reviews. Weaker specs, but less chance to overheat. Also, all the IoT project reports used older models, so RPI4 isn't needed. Missing some items (like MicroSD card)
HXT 5010 Servo Motor (Rotary Actuator) | 2 | $10.18 | HobbyKing (https://hobbyking.com/en_us/hxt-5010-twin-bearing-digital-servo-6-9kg-0-16sec-39-2g.html) | Cheap, lightweight. Provides large amount of torque without sacrificing speed. Allows precise control of angular position. Buy an extra as a spare.
Sharp GP2Y0A51SK0F Analog Distance Sensor | 2 | $23.90 | RobotShop (https://www.robotshop.com/en/sharp-gp2y0a51sk0f-analog-distance-sensor-2cm-15cm.html) | Short-range (2-15cm) distance sensor. To detect when the door is locked/unlocked, point it at the door knob. When it moves position slightly, it will sense the change in states. To detect when the door is opened, point it at the door itself.
Heavy Duty Removeable Double-Sided Mounting Tape | 1 | $6.99 | Amazon (https://www.amazon.com/Double-Sided-Tape-Heavy-Duty/dp/B07FVHZHJY) | Used to mount the lock onto the door. First, the double-sided tape is placed on the door, so you can easily remove it without damaging the surface.
VELCRO Adhesive Strips | 2 | $13.58 | Amazon (https://www.amazon.com/VELCRO-Brand-Industrial-Fasteners-Professional/dp/B0010HADEA?pd_) | The Velcro is used to fasten the lock to the mounting tape. Supports up to 10lbs
AmazonBasics Deadbolt - | 1 | $12.39 | Amazon (https://www.amazon.com/gp/cart/view.html?ref_=nav_cart) | Testing Object
Total |  | $137.03

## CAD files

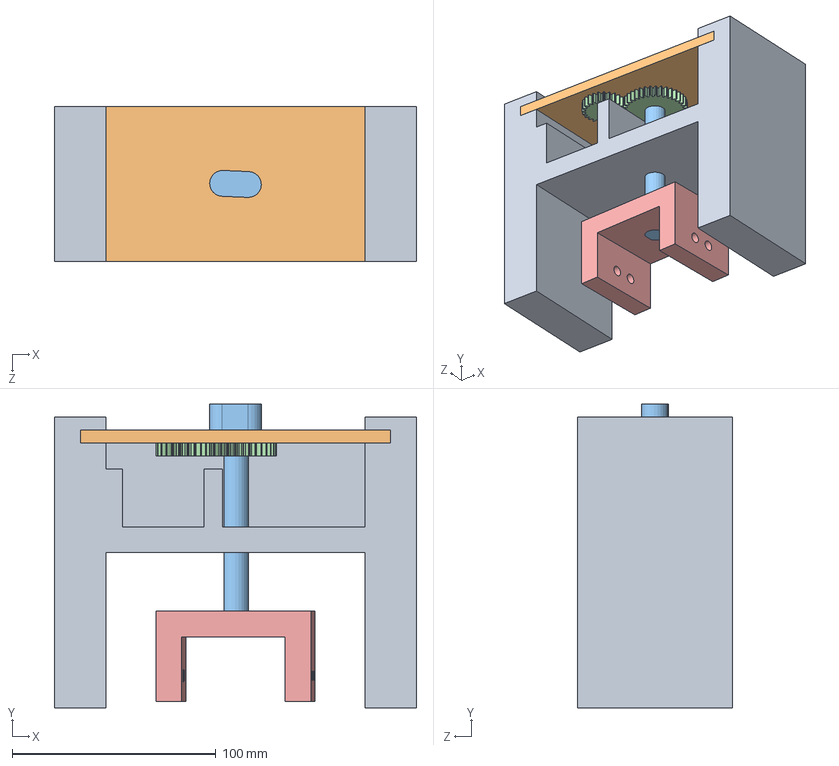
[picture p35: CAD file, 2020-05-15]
demos/CAD/Assem1.SLDASM
177.8 x 149.1 x 76.3 mm
Base
Cover
Shaft
spur gear_ai x 2
clamp

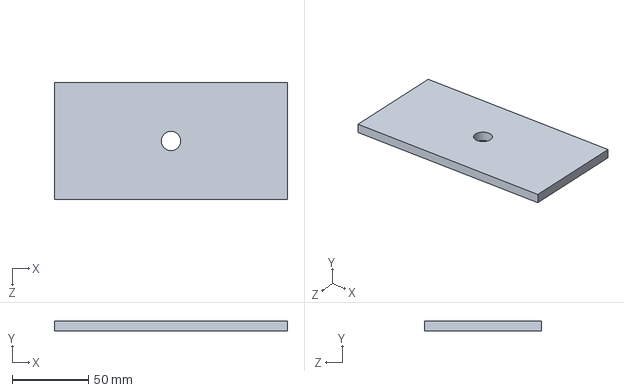
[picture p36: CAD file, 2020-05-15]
demos/CAD/Cover.SLDPRT
152.4 x 6.35 x 76.2 mm

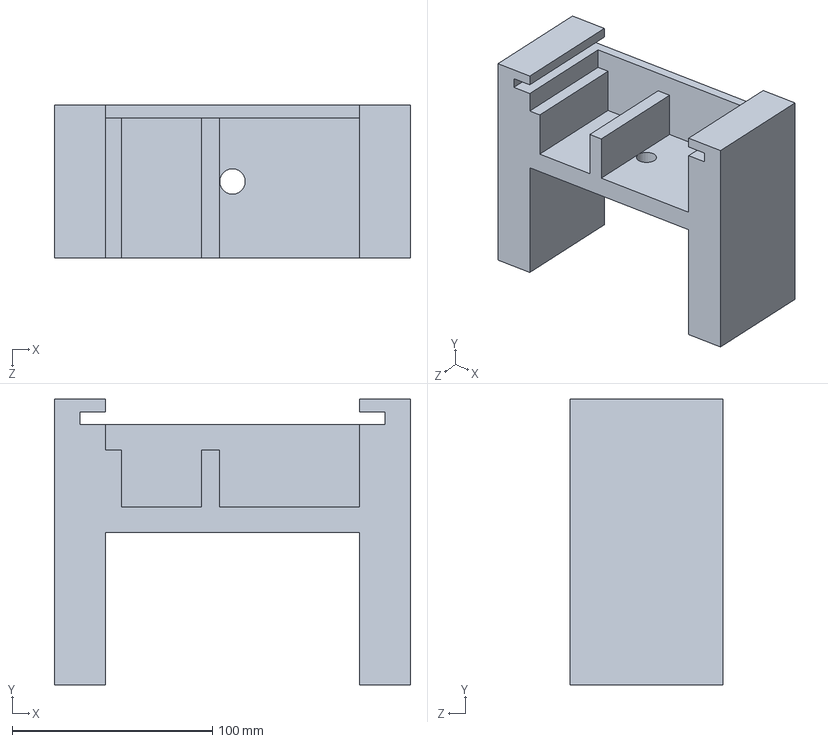
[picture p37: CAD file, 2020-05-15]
demos/CAD/Base.SLDPRT
177.8 x 142.8 x 76.2 mm

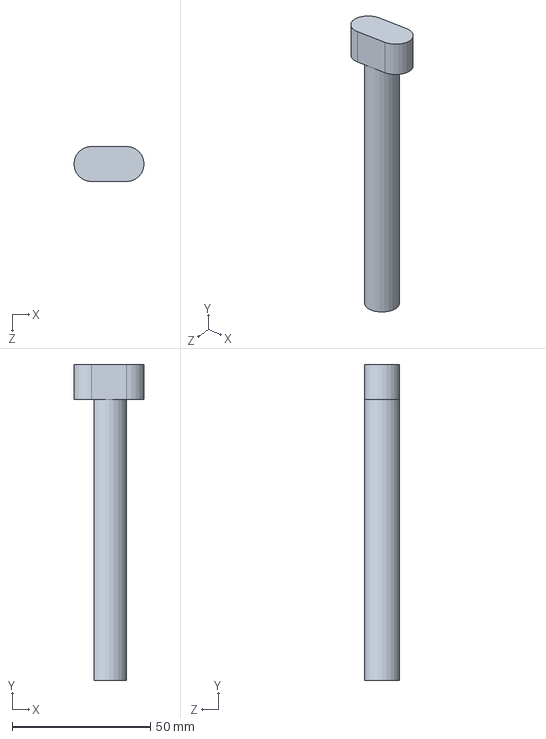
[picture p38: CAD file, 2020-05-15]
demos/CAD/Shaft.SLDPRT
25.4 x 114.3 x 12.7 mm

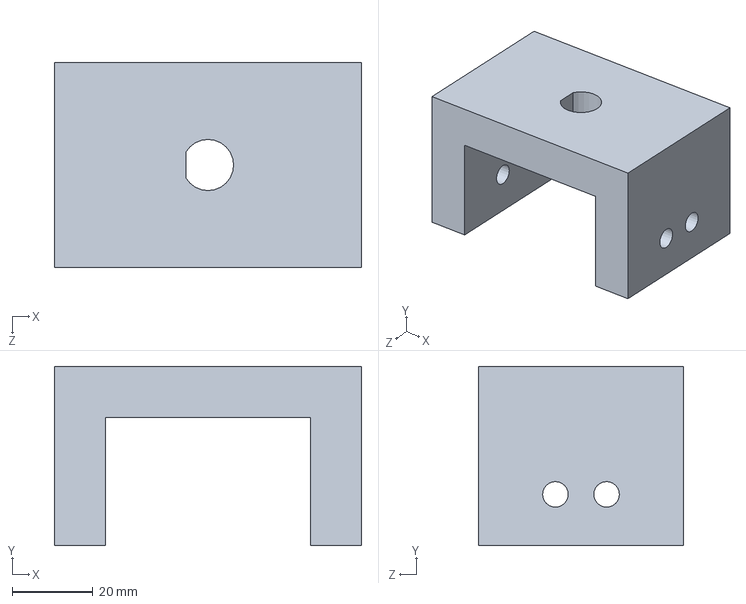
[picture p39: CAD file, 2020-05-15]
demos/CAD/clamp.SLDPRT
76.2 x 44.5 x 50.8 mm

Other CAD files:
demos/CAD/Assem1.SLDDRW

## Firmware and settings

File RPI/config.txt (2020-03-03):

Raspberry Pi login
Username: pi
Password: dobby

MySQL Server login
Username: root
Password: dobby

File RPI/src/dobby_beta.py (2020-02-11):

import RPi.GPIO as GPIO
import time

#5V(red) -> pin 4
#GND(black) -> pin 6
#servo motor -> pin 11 (GPIO17)

servoPIN = 11

GPIO.setmode(GPIO.BOARD)

GPIO.setup(servoPIN, GPIO.OUT)

p = GPIO.PWM(servoPIN, 50)

#servo having 20ms cycles, dc=0.5/20 X100 = 2.5% ->90degree

p.start(5) #initialization, 0degree

try:
    while True:
        p.ChangeDutyCycle(7.5)  # turn towards 90 degree
        time.sleep(1) # sleep 1 second
        p.ChangeDutyCycle(5)  # turn towards 0 degree
        time.sleep(1) # sleep 1 second
        p.ChangeDutyCycle(10) # turn towards 180 degree
        time.sleep(1) # sleep 1 second 

except KeyboardInterrupt:
    p.stop()
    GPIO.cleanup()

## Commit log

2020-02-18 added design documents
    [config.txt]
2020-03-03 minor changes
    [config.txt]
2021-01-20 added docs, reorganized
    [Assem1.SLDASM, Assem1.SLDDRW, Base.SLDPRT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]
